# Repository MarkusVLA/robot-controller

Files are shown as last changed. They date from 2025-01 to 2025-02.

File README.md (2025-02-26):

# Robot Controller

## Overview
ESP32-S3 based robot controller designed for combat robots in the 150g weight class

The controller can control 2 DC-motors for vehicle movement and an ESC for the main weapon. The board also embeds a 3-axis gyroscope and accelerometer which can be used to improve vehicle handling or detect when the robot is flipped. Wireless control is enabled through an integrated 2.4GHz PCB-antenna supporting both WiFi and Bluetooth. 

## Schematic and Layout

<div style="display: flex; gap: 20px;">
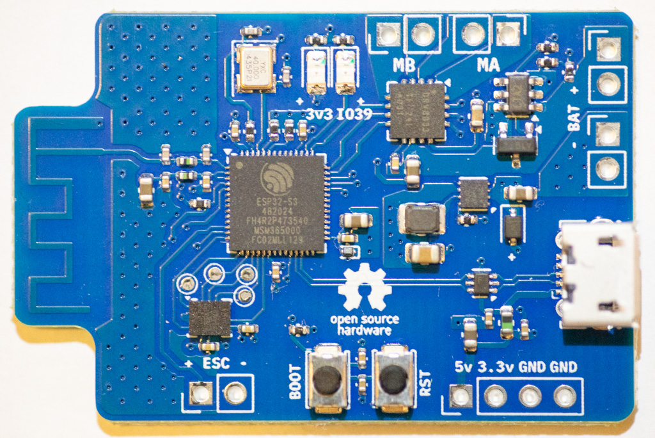
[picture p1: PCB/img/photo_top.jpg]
3D render of the top side
    
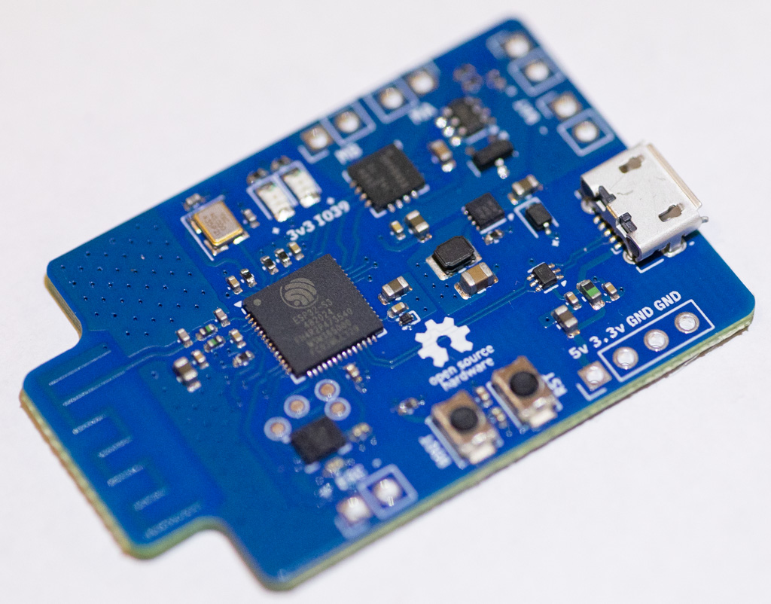
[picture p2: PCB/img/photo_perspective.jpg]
3D render perspective view
    
</div>

[View Schematic (PDF)](documentation/schematic.pdf)

## Firmware
The esp32 firmware is being developed in C using the ESP-IDF framework.
Installation and build instructions from: [ESP-IDF API reference](https://docs.espressif.com/projects/esp-idf/en/stable/esp32/api-reference/index.html)

[Comprehensive hardware documentation](documentation/Hardware_documentation.pdf)

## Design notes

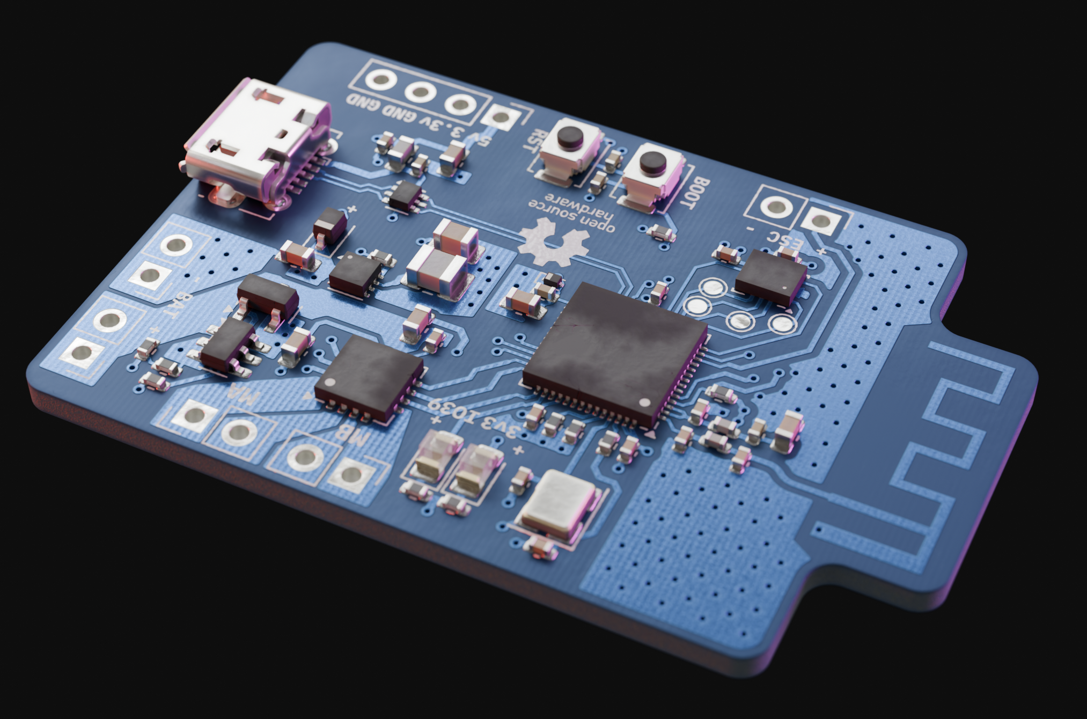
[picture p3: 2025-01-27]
PCB/img/render.png

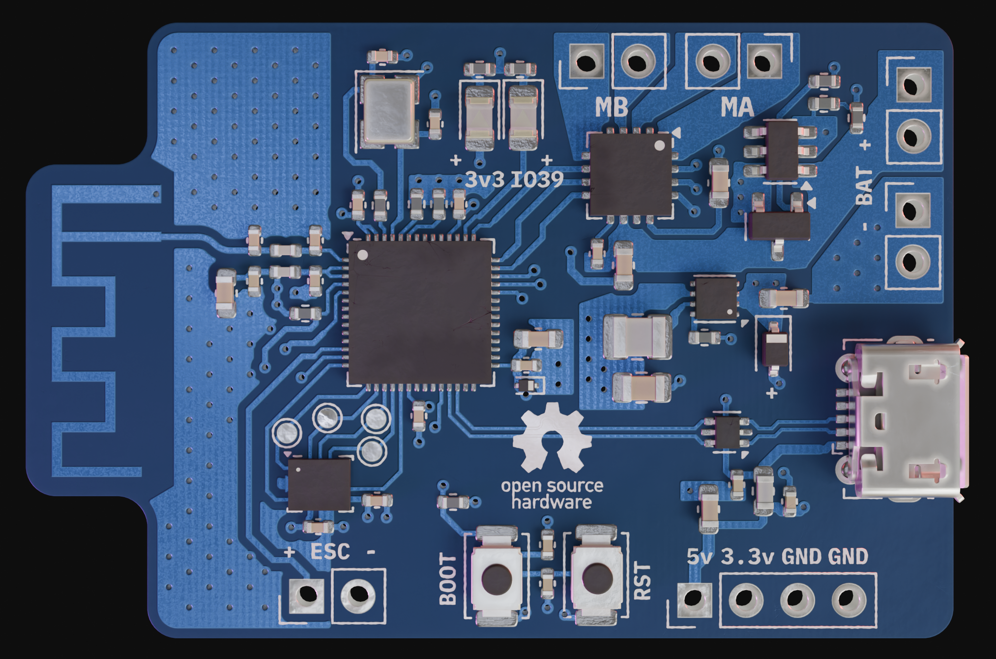
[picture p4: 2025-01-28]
PCB/img/render_top.png

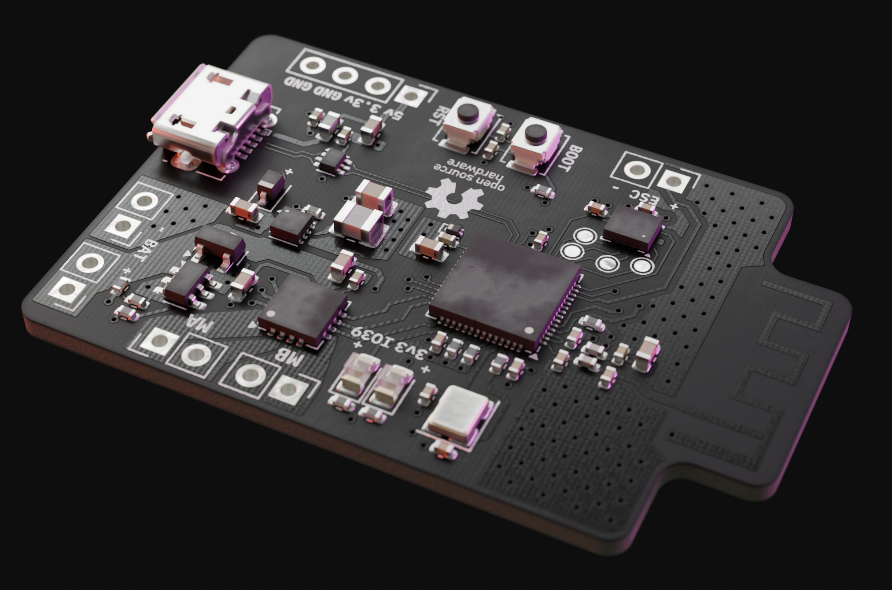
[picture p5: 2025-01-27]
PCB/img/render2.png

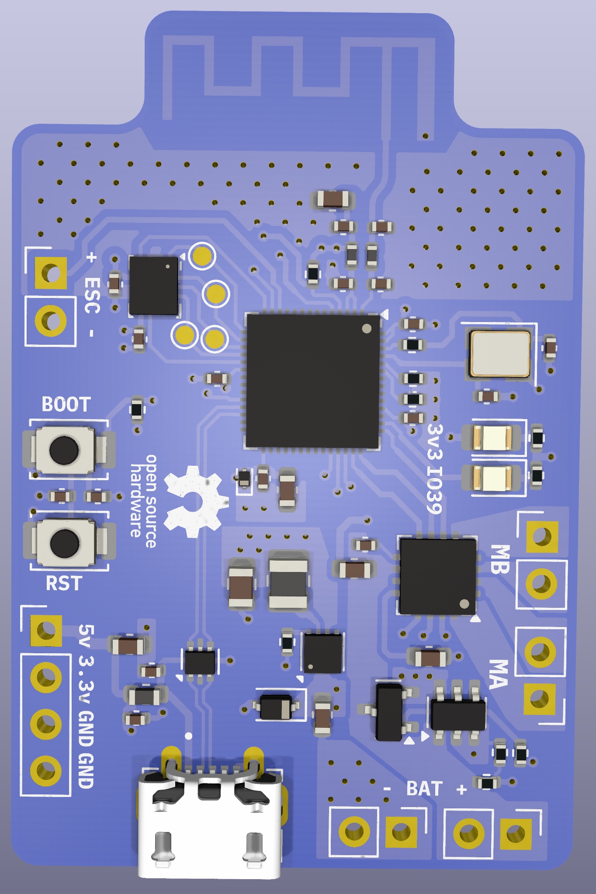
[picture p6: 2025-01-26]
PCB/img/layout.jpg

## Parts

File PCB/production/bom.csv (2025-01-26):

Designator | Footprint | Quantity | Value | LCSC Part #
AE2 | Texas_SWRA117D_2.4GHz_Left | 1 | Antenna_Shield
C1, C13, C14, C2, C30, C32, C33, C35, C36, C37, C8, C9 | 0402 | 12 | 100n
C10, C12, C34, C39, C5 | 0603 | 5 | 10u
C11 | 0603 | 1 | 2.2u
C27, C28 | 0402 | 2 | 22p
C29, C31 | 0402 | 2 | 3.3p
C6 | 0805 | 1 | 22u
C7 | 0402 | 1 | 10n
D1, D4 | 0805 | 2 | LED | C205445
D3 | D_SOD-323 | 1 | BAT60A
D5 | D_SOD-923 | 1 | SZESD9B5.0ST5G
J1 | USB_Micro-B_Molex-105017-0001 | 1 | USB_B_Micro
J10, J3, J4, J5, J6 | PinHeader_1x02_P2.54mm_Vertical | 5 | Conn_01x02
J2 | PinHeader_1x04_P2.54mm_Vertical | 1 | Conn_01x04
L1 | 1008 | 1 | 2.2u
L2 | 0603 | 1 | 2.2n
L5, L6 | 0402 | 2 | 2.2n
Q1 | SOT-23 | 1 | AO3401A
R1, R5 | 0402 | 2 | 1k | C163928
R12 | 0402 | 1 | 10
R13, R14, R2, R7, R8 | 0402 | 5 | 10k
R3 | 0402 | 1 | 470k
R4 | 0402 | 1 | 100k
R6 | 0402 | 1 | 15k
SW3 | SW_Push_SPST_NO_Alps_SKRK | 1 | Reset | C115357
SW4 | SW_Push_SPST_NO_Alps_SKRK | 1 | Boot | C115357
TP1, TP2, TP3, TP4 | TestPoint_Pad_D1.0mm | 4 | TestPoint
U1 | LGA-14_3x2.5mm_P0.5mm_LayoutBorder3x4y | 1 | LSM6DS3
U2 | TSOT-23-6 | 1 | LTC4412xS6
U3 | SOT-666 | 1 | USBLC6-2P6
U4 | WSON-8-1EP_2x2mm_P0.5mm_EP0.9x1.6mm_ThermalVias | 1 | TPS62172DSG
U5 | Texas_RTY_WQFN-16-1EP_4x4mm_P0.65mm_EP2.1x2.1mm_ThermalVias | 1 | DRV8833RTY
U7 | QFN-56-1EP_7x7mm_P0.4mm_EP5.6x5.6mm | 1 | ESP32-S3
Y2 | Crystal_SMD_3225-4Pin_3.2x2.5mm | 1 | 40MHz

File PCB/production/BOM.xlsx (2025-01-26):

Designator | Footprint | Quantity | Value | LCSC Part #
C1, C13, C14, C2, C30, C32, C33, C35, C36, C37, C8, C9 | 402 | 12 | 100n | C1525
C10, C12, C34, C39, C5 | 603 | 5 | 10u | C70225
C11 | 603 | 1 | 2.2u | C57895
C27, C28 | 402 | 2 | 22p | C1555
C29, C31 | 402 | 2 | 3.3p | C57895
C6 | 805 | 1 | 22u | C45783
C7 | 402 | 1 | 10n | C15195
D1, D4 | 805 | 2 | LED | C2295
D3 | D_SOD-323 | 1 | BAT60A | C3018529
D5 | D_SOD-923 | 1 | SZESD9B5.0ST5G | C328101
J1 | CUI_UJ2-MIBH2-4-SMT-TR | 1 | UJ2-MIBH2-4-SMT-TR | C91146
L1 | 1008 | 1 | 2.2u | C23894
L2 | 603 | 1 | 2.2n | C113061
L5, L6 | 402 | 2 | 2.2n | C86061
Q1 | SOT-23 | 1 | AO3401A | C181091
R1, R5 | 402 | 2 | 1k | C11702
R12 | 402 | 1 | 10 | C159870
R13, R14, R2, R7, R8 | 402 | 5 | 10k | C25531
R3 | 402 | 1 | 470k | C25562
R4 | 402 | 1 | 100k | C25741
R6 | 402 | 1 | 15k | C25543
SW3 | SW_Push_SPST_NO_Alps_SKRK | 1 | Reset | C115357
SW4 | SW_Push_SPST_NO_Alps_SKRK | 1 | Boot | C115357
U1 | LGA-14_3x2.5mm_P0.5mm_LayoutBorder3x4y | 1 | LSM6DS3 | C95230
U2 | TSOT-23-6 | 1 | LTC4412xS6 | C514442
U3 | SOT-666 | 1 | USBLC6-2P6 | C15999
U4 | WSON-8-1EP_2x2mm_P0.5mm_EP0.9x1.6mm_ThermalVias | 1 | TPS62172DSG | C59873
U5 | Texas_RTY_WQFN-16-1EP_4x4mm_P0.65mm_EP2.1x2.1mm_ThermalVias | 1 | DRV8833RTY | C154936
U7 | QFN-56-1EP_7x7mm_P0.4mm_EP5.6x5.6mm | 1 | ESP32-S3 | C3013940
Y2 | Crystal_SMD_3225-4Pin_3.2x2.5mm | 1 | 40MHz | C9010

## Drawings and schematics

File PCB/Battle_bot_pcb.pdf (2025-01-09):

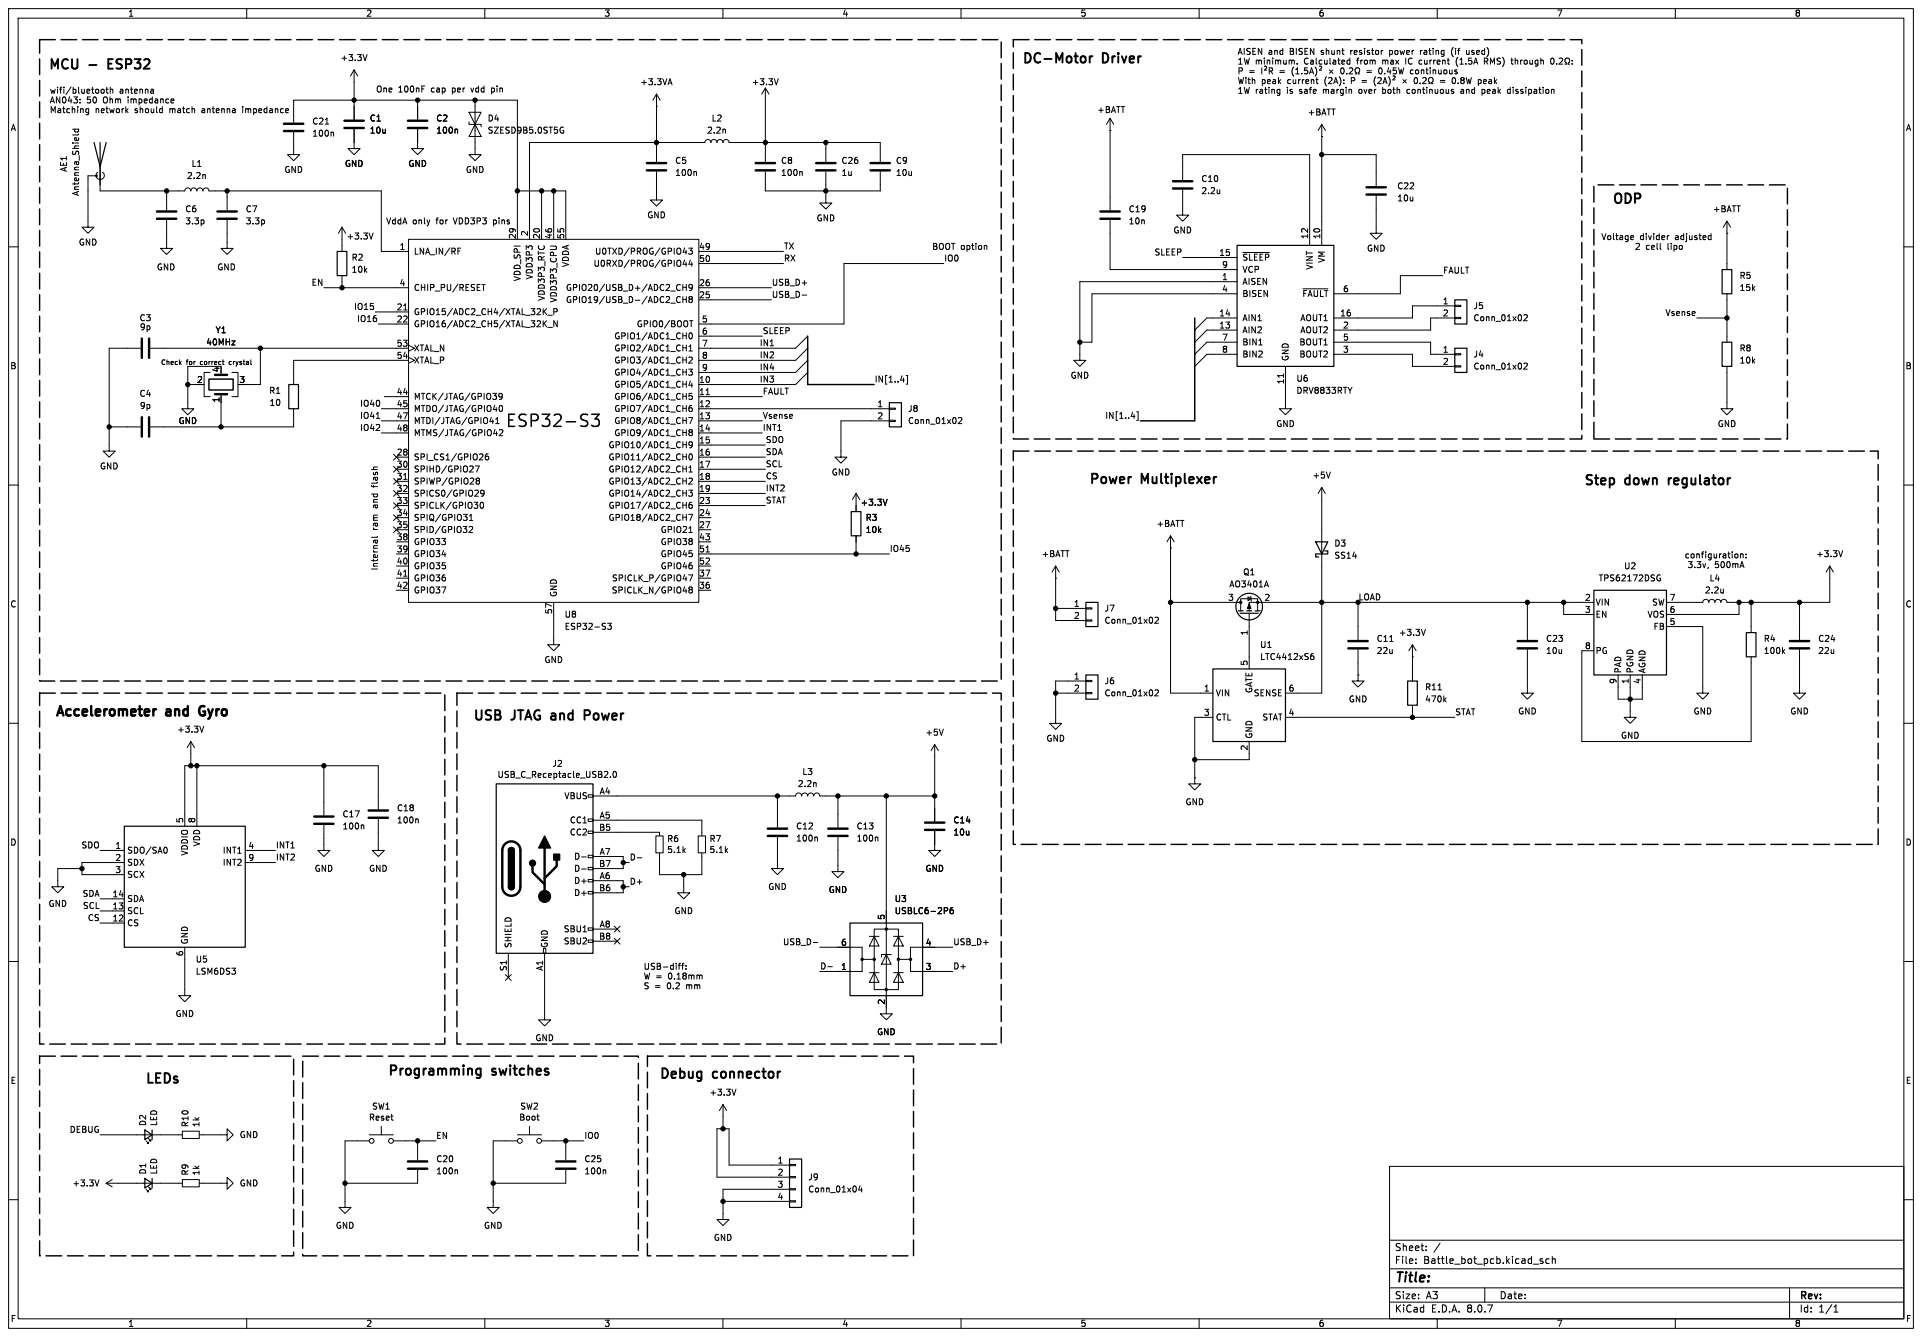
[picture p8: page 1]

One 100nF cap per vdd pin C1

Matching network should match antenna impedance

VddA only for VDD3P3 pins

2 VDD3P3_RTC 20 GPIO15/ADC2_CH4/XTAL_32K_P 21 GPIO16/ADC2_CH5/XTAL_32K_N 22 GPIO17/ADC2_CH6 23 GPIO18/ADC2_CH7 24 GPIO19/USB_D-/ADC2_CH8 25 GPIO20/USB_D+/ADC2_CH9 26 GPIO21 27 SPI_CS1/GPIO26 28 VDD_SPI 29 SPIHD/GPIO27 30 SPIWP/GPIO28 31 SPICS0/GPIO29 32 SPICLK/GPIO30 33 SPIQ/GPIO31 34 SPID/GPIO32 35 GPIO33 38 GPIO34 39 CHIP_PU/RESET 4 GPIO35 40 GPIO36 41 GPIO37 42 GPIO38 43 MTCK/JTAG/GPIO39 44 MTDO/JTAG/GPIO40 45 VDD3P3_CPU 46 MTDI/JTAG/GPIO41 47 MTMS/JTAG/GPIO42 48 U0TXD/PROG/GPIO43 49 GPIO0/BOOT 5 U0RXD/PROG/GPIO44 50 GPIO45 51 GPIO46 52 XTAL_N 53 XTAL_P 54 VDDA 55 GND 57 GPIO1/ADC1_CH0 6 GPIO2/ADC1_CH1 7 GPIO3/ADC1_CH2 8 GPIO4/ADC1_CH3 9 U8ESP32-S3

S = 0.2 mm Debug connector Internal ram and flash

SDO/SA0 1 CS 12 SCL 13 SDA 14 SDX 2 SCX 3

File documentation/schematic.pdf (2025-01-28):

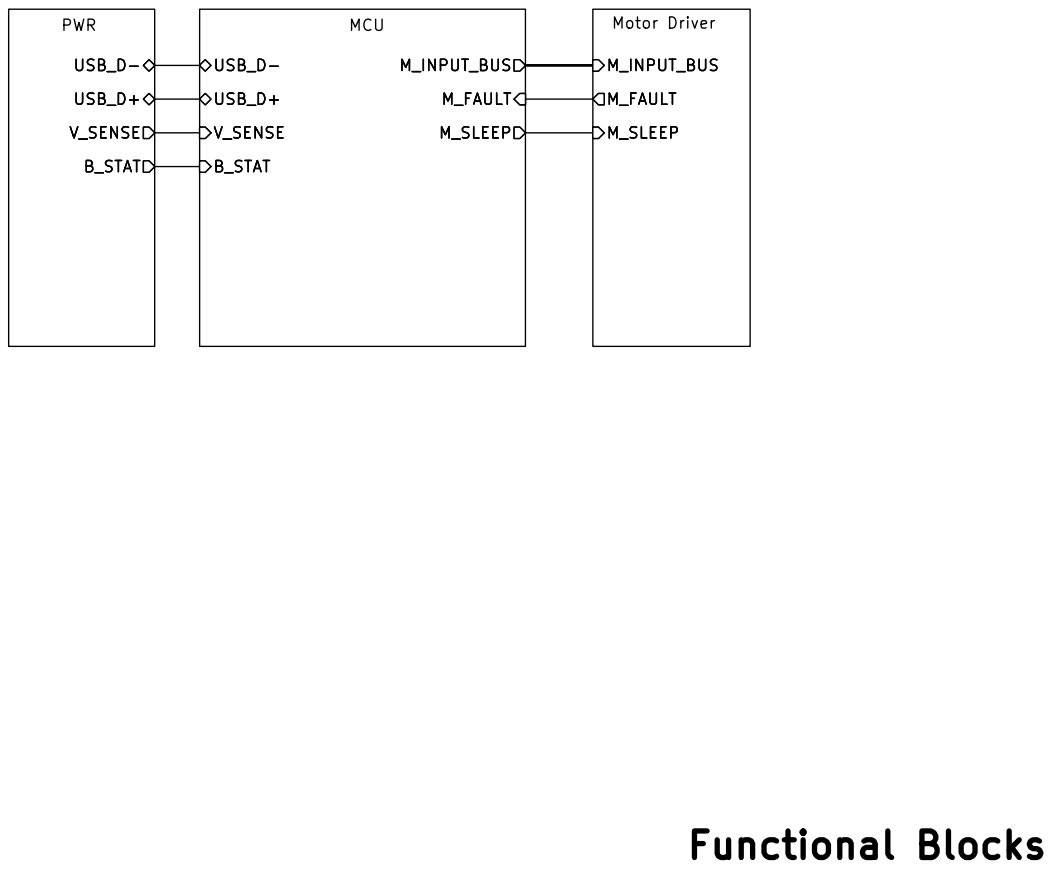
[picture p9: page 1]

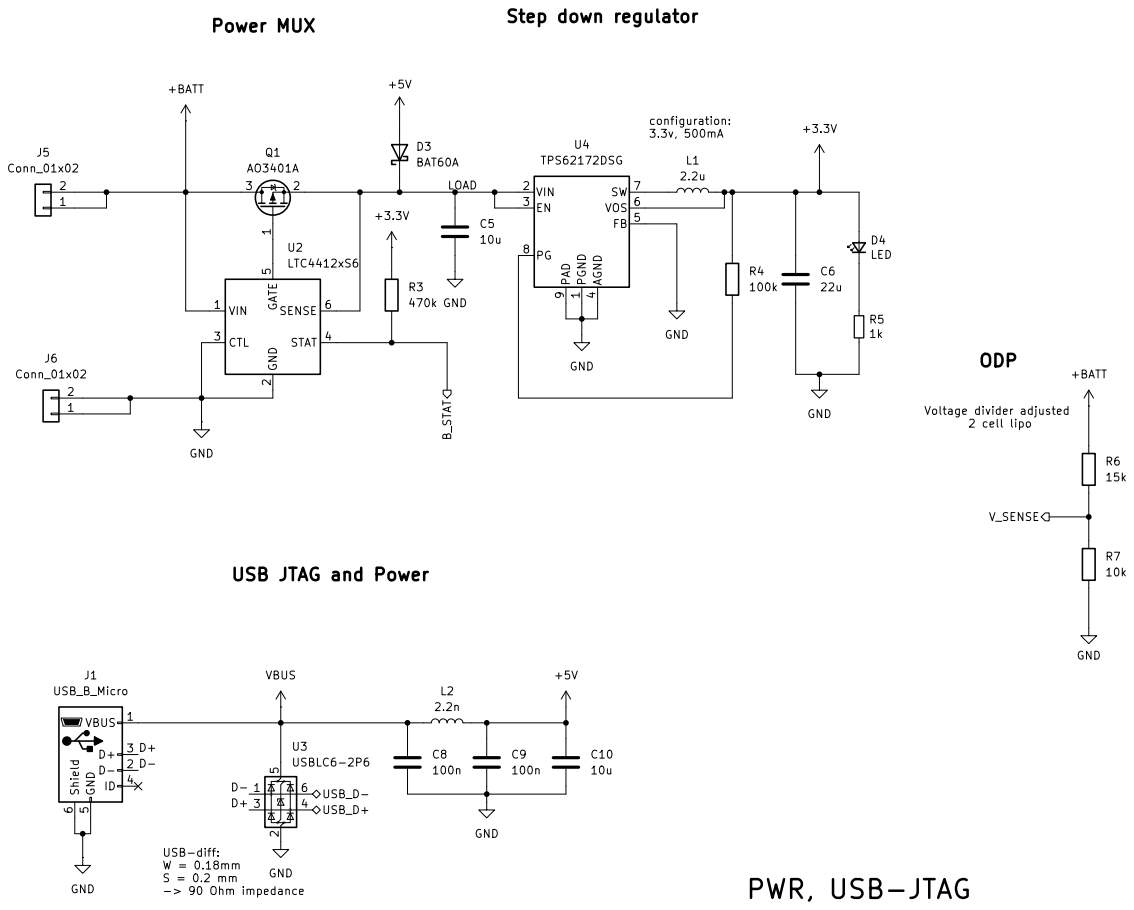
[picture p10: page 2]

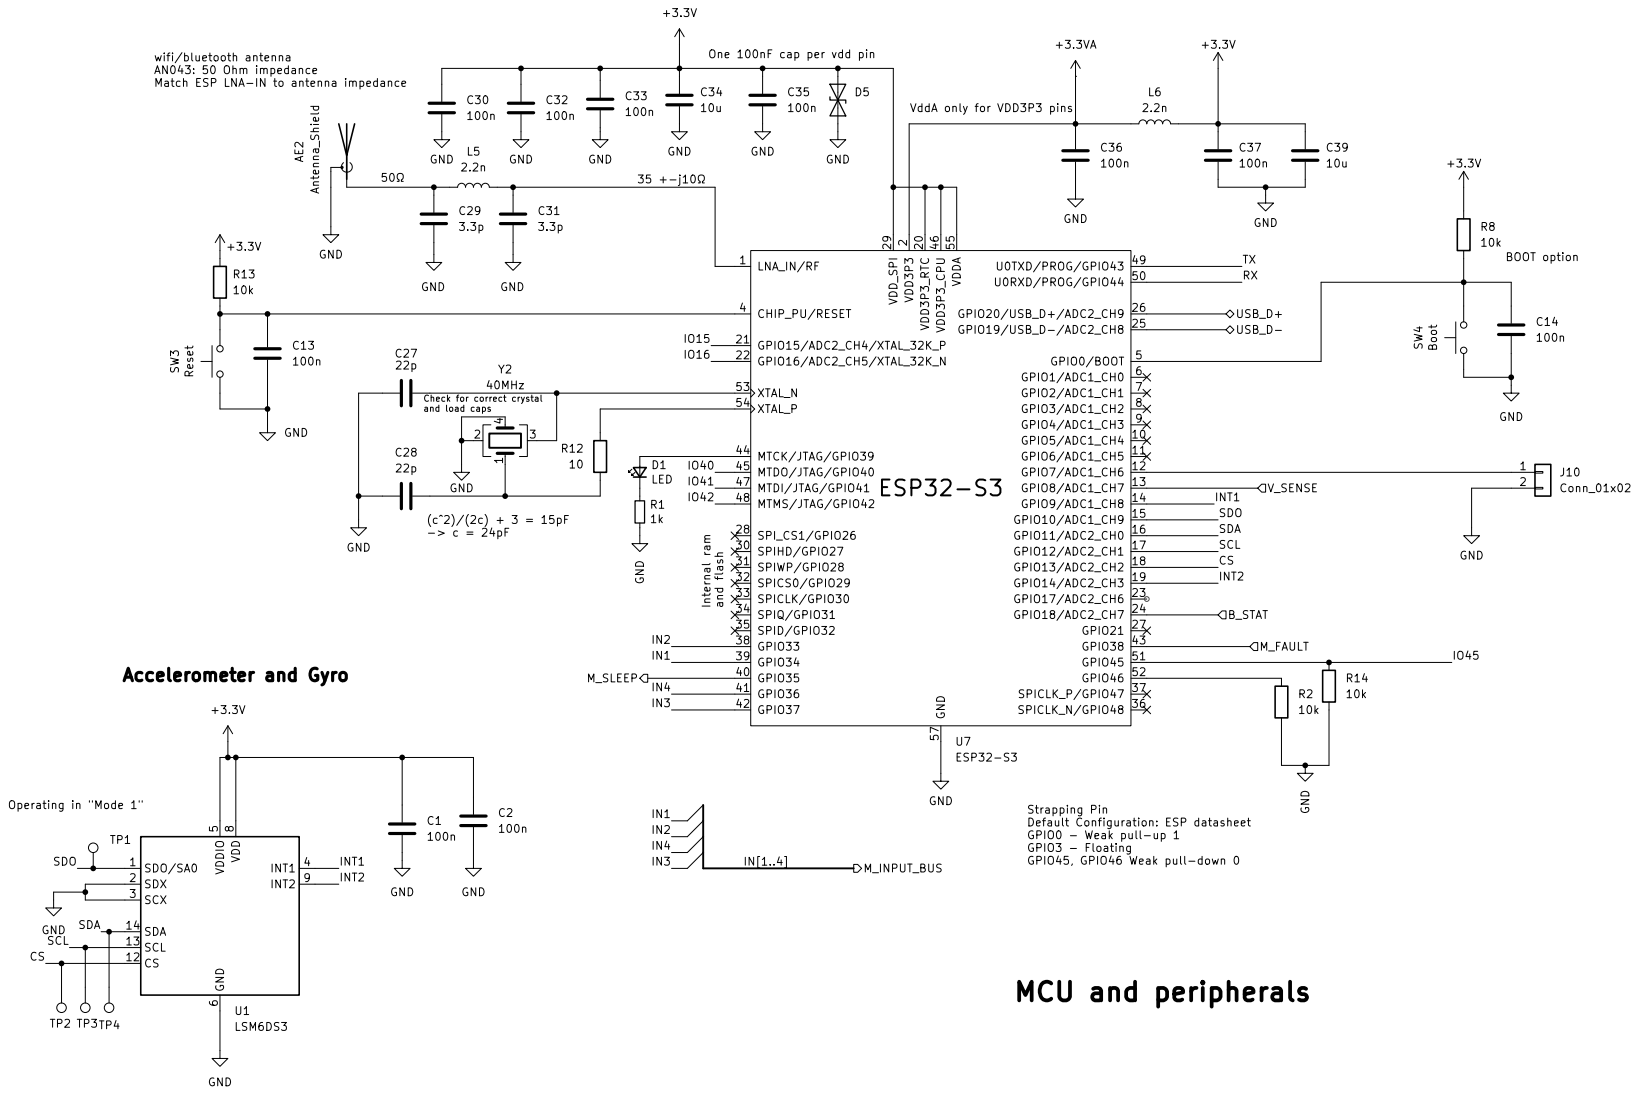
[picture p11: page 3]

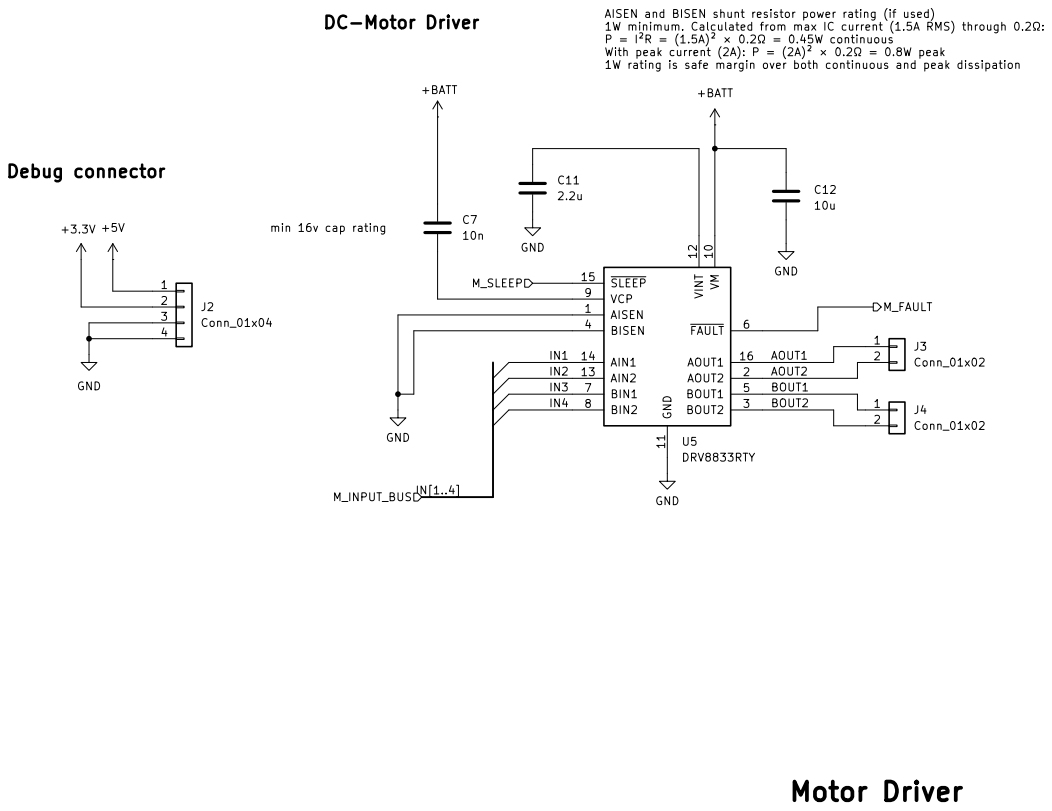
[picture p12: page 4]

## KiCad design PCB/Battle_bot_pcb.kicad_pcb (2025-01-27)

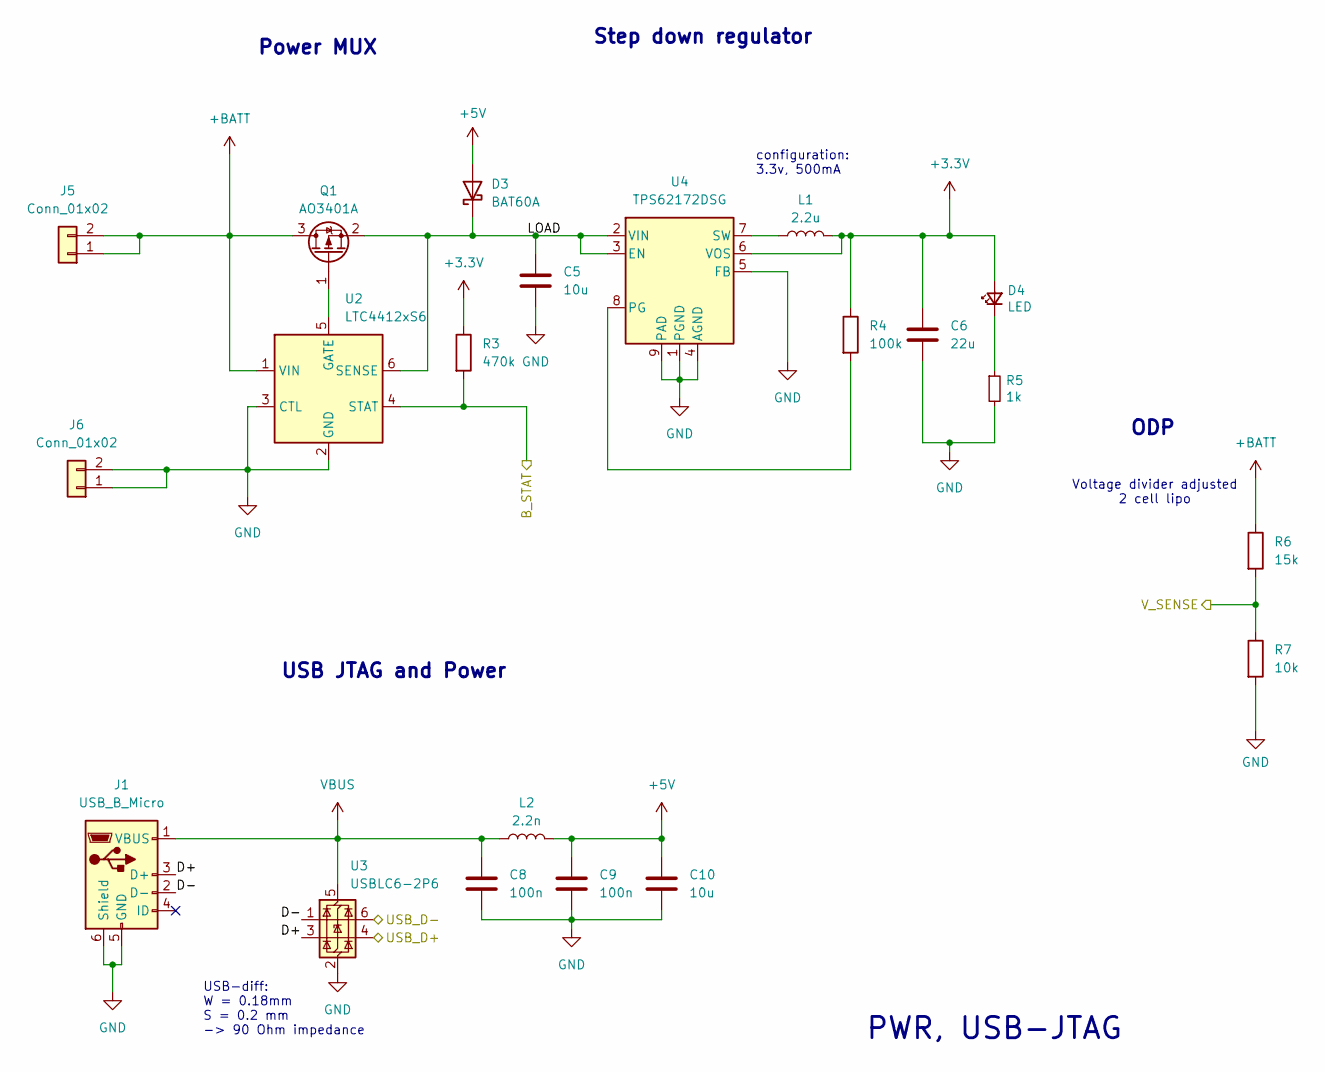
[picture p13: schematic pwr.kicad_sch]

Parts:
C5, C10: 10u; C_0603_1608Metric
C6: 22u; C_0805_2012Metric
C8, C9: 100n; C_0402_1005Metric
D3: BAT60A; D_SOD-323
D4: LED; LED_0805_2012Metric_Pad1.15x1.40mm_HandSolder; LCSC C205445
J1: USB_B_Micro; USB_Micro-B_Molex-105017-0001
J5, J6: Conn_01x02; PinHeader_1x02_P2.54mm_Vertical
L1: 2.2u; L_1008_2520Metric
L2: 2.2n; L_0603_1608Metric
Q1: AO3401A; SOT-23
R3: 470k; R_0402_1005Metric
R4: 100k; R_0402_1005Metric
R5: 1k; R_0402_1005Metric; LCSC C163928
R6: 15k; R_0402_1005Metric
R7: 10k; R_0402_1005Metric
U2: LTC4412xS6; TSOT-23-6
U3: USBLC6-2P6; SOT-666
U4: TPS62172DSG; WSON-8-1EP_2x2mm_P0.5mm_EP0.9x1.6mm_ThermalVias

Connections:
+3.3V: C6.1, D4.2 (A), L1.2, R3.1, R4.1, U4.6 (VOS); also elsewhere on the board
+5V: C9.1, C10.1, D3.2 (A), L2.2; also elsewhere on the board
+BATT: J5.1, J5.2, Q1.3 (D), R6.1, U2.1 (VIN); also elsewhere on the board
/MCU/B_STAT: R3.2, U2.4 (STAT); also elsewhere on the board
/MCU/USB_D+: U3.4 (I/O2); also elsewhere on the board
/MCU/USB_D-: U3.6 (I/O1); also elsewhere on the board
/MCU/V_SENSE: R6.2, R7.1; also elsewhere on the board
/PWR/D+: J1.3 (D+), U3.3 (I/O2)
/PWR/D-: J1.2 (D-), U3.1 (I/O1)
/PWR/LOAD: C5.1, D3.1 (K), Q1.2 (S), U2.6 (SENSE), U4.2 (VIN), U4.3 (EN)
GND: C5.2, C6.2, C8.2, C9.2, C10.2, J1.5 (GND), J1.6 (Shield), J6.1, J6.2, R5.2, R7.2, U2.2 (GND), U2.3 (CTL), U3.2 (GND), U4.1 (PGND), U4.4 (AGND), U4.5 (FB), U4.9 (PAD); also elsewhere on the board
unnamed: D4.1 (K), R5.1
unnamed: Q1.1 (G), U2.5 (GATE)
unnamed: R4.2, U4.8 (PG)
unnamed: L1.1, U4.7 (SW)
VBUS: C8.1, J1.1 (VBUS), L2.1, U3.5 (VBUS)

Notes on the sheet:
Power MUX
USB JTAG and Power
ODP
USB-diff: W = 0.18mm S = 0.2 mm -> 90 Ohm impedance
configuration: 3.3v, 500mA
PWR, USB-JTAG
Voltage divider adjusted 2 cell lipo
Step down regulator

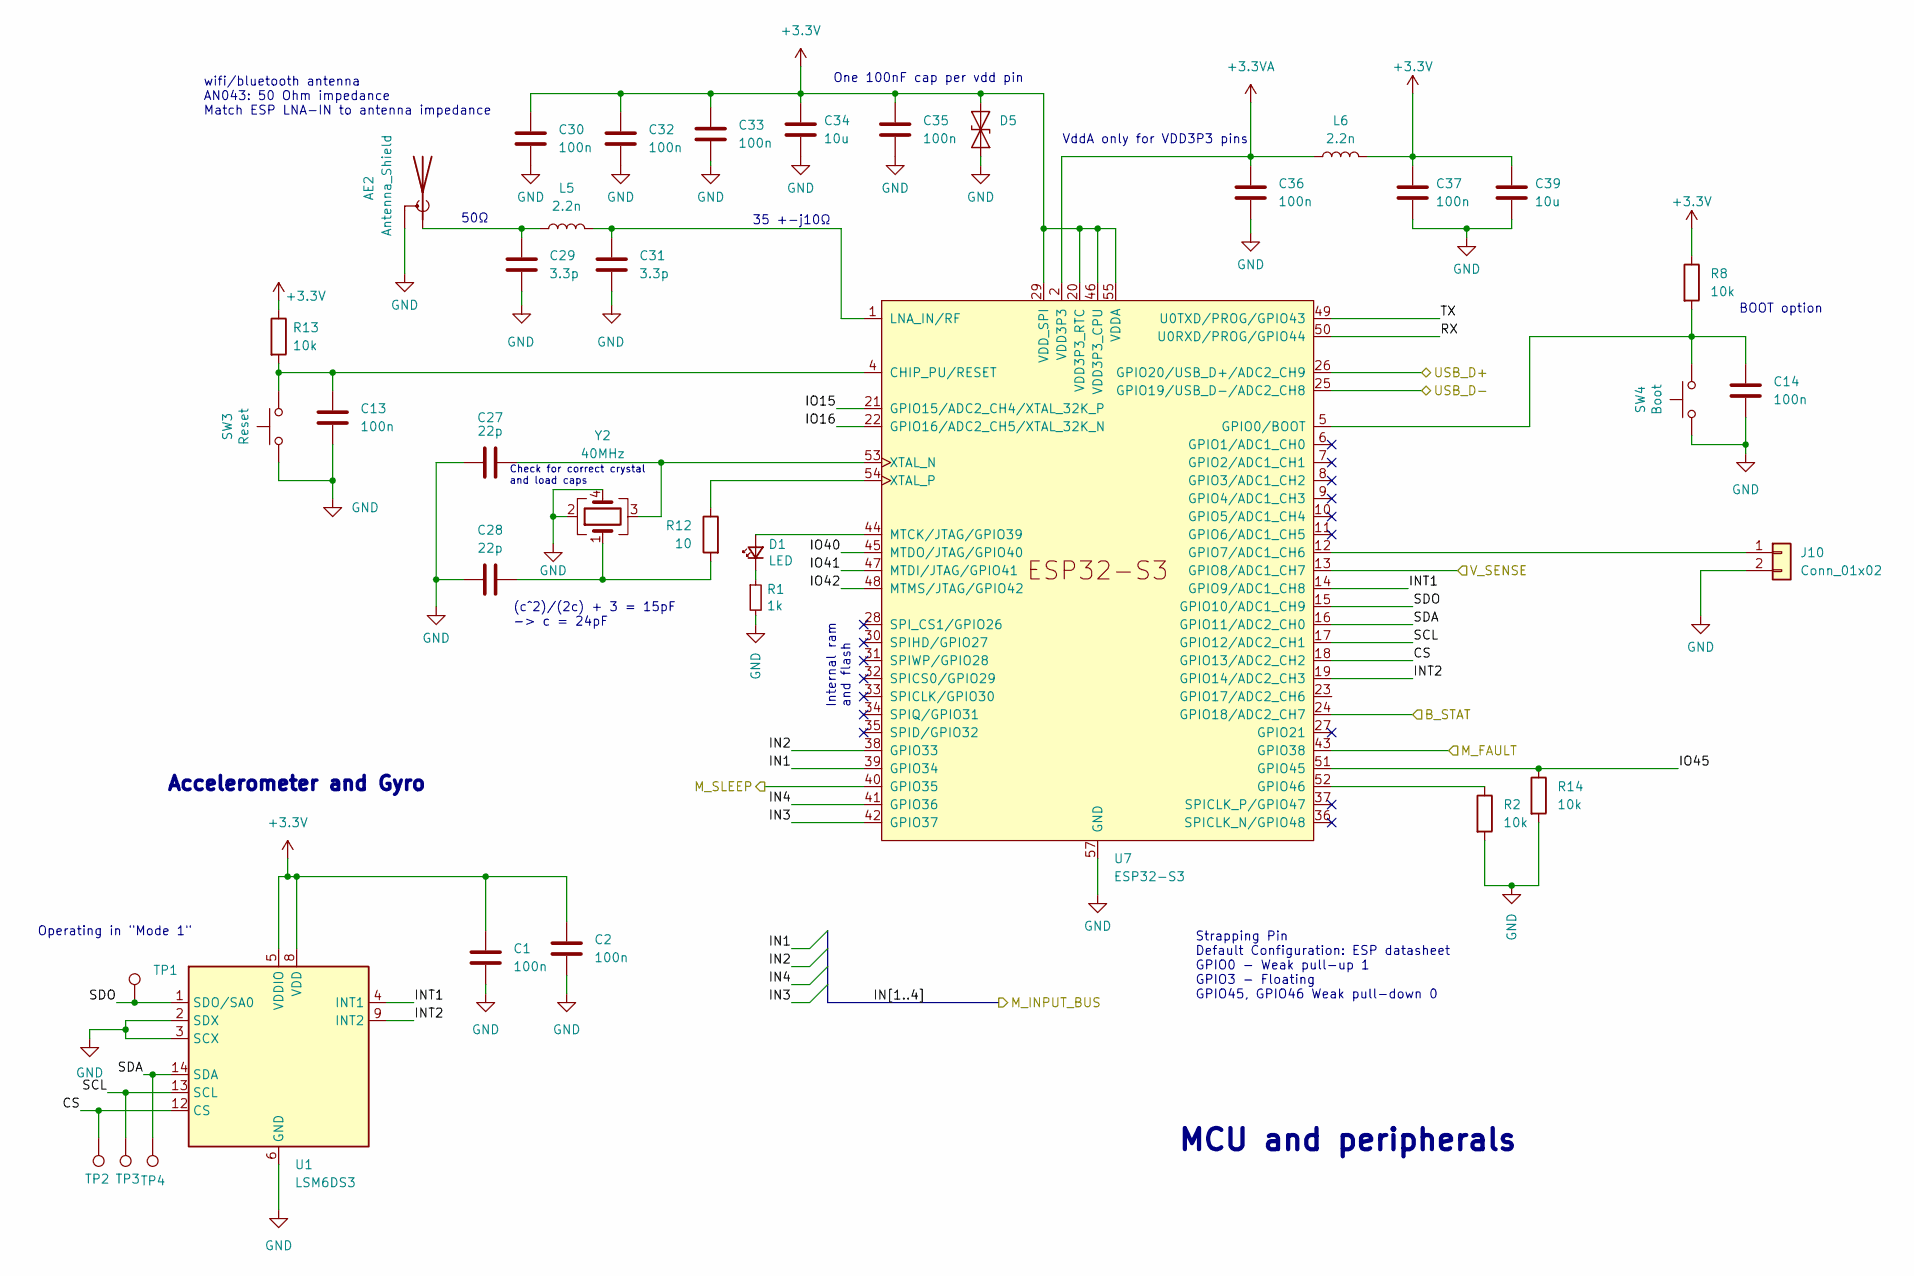
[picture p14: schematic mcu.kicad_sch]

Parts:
AE2: Antenna_Shield; Texas_SWRA117D_2.4GHz_Left
C1, C2, C13, C14, C30, C32, C33, C35, C36, C37: 100n; C_0402_1005Metric
C27, C28: 22p; C_0402_1005Metric
C29, C31: 3.3p; C_0402_1005Metric
C34, C39: 10u; C_0603_1608Metric
D1: LED; LED_0805_2012Metric_Pad1.15x1.40mm_HandSolder; LCSC C205445
D5: SZESD9B5.0ST5G; D_SOD-923
J10: Conn_01x02; PinHeader_1x02_P2.54mm_Vertical
L5, L6: 2.2n; L_0402_1005Metric
R1: 1k; R_0402_1005Metric; LCSC C163928
R2, R8, R13, R14: 10k; R_0402_1005Metric
R12: 10; R_0402_1005Metric
SW3: Reset; SW_Push_SPST_NO_Alps_SKRK; LCSC C115357
SW4: Boot; SW_Push_SPST_NO_Alps_SKRK; LCSC C115357
TP1, TP2, TP3, TP4: TestPoint; TestPoint_Pad_D1.0mm
U1: LSM6DS3; LGA-14_3x2.5mm_P0.5mm_LayoutBorder3x4y
U7: ESP32-S3; QFN-56-1EP_7x7mm_P0.4mm_EP5.6x5.6mm
Y2: 40MHz; Crystal_SMD_3225-4Pin_3.2x2.5mm

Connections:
+3.3V: C1.1, C2.1, C30.1, C32.1, C33.1, C34.1, C35.1, C37.1, C39.1, D5.2 (A2), L6.2, R8.1, R13.1, U1.5 (VDDIO), U1.8 (VDD), U7.20 (VDD3P3_RTC), U7.29 (VDD_SPI), U7.46 (VDD3P3_CPU), U7.55 (VDDA), U7.56 (VDDA); also elsewhere on the board
+3.3VA: C36.1, L6.1, U7.2 (VDD3P3), U7.3 (VDD3P3)
/IO/IN1: U7.39 (GPIO34); also elsewhere on the board
/IO/IN2: U7.38 (GPIO33); also elsewhere on the board
/IO/IN3: U7.42 (GPIO37); also elsewhere on the board
/IO/IN4: U7.41 (GPIO36); also elsewhere on the board
/IO/M_FAULT: U7.43 (GPIO38); also elsewhere on the board
/IO/M_SLEEP: U7.40 (GPIO35); also elsewhere on the board
/MCU/B_STAT: U7.24 (GPIO18/ADC2_CH7); also elsewhere on the board
/MCU/CS: TP2.1, U1.12 (CS), U7.18 (GPIO13/ADC2_CH2)
/MCU/INT1: U1.4 (INT1), U7.14 (GPIO9/ADC1_CH8)
/MCU/INT2: U1.9 (INT2), U7.19 (GPIO14/ADC2_CH3)
/MCU/IO15: U7.21 (GPIO15/ADC2_CH4/XTAL_32K_P)
/MCU/IO16: U7.22 (GPIO16/ADC2_CH5/XTAL_32K_N)
/MCU/IO40: U7.45 (MTDO/JTAG/GPIO40)
/MCU/IO41: U7.47 (MTDI/JTAG/GPIO41)
/MCU/IO42: U7.48 (MTMS/JTAG/GPIO42)
/MCU/IO45: R14.1, U7.51 (GPIO45)
/MCU/RX: U7.50 (U0RXD/PROG/GPIO44)
/MCU/SCL: TP3.1, U1.13 (SCL), U7.17 (GPIO12/ADC2_CH1)
/MCU/SDA: TP4.1, U1.14 (SDA), U7.16 (GPIO11/ADC2_CH0)
/MCU/SDO: TP1.1, U1.1 (SDO/SA0), U7.15 (GPIO10/ADC1_CH9)
/MCU/TX: U7.49 (U0TXD/PROG/GPIO43)
/MCU/USB_D+: U7.26 (GPIO20/USB_D+/ADC2_CH9); also elsewhere on the board
/MCU/USB_D-: U7.25 (GPIO19/USB_D-/ADC2_CH8); also elsewhere on the board
/MCU/V_SENSE: U7.13 (GPIO8/ADC1_CH7); also elsewhere on the board
GND: AE2.2 (Shield), C1.2, C2.2, C13.2, C14.2, C27.1, C28.1, C29.2, C30.2, C31.2, C32.2, C33.2, C34.2, C35.2, C36.2, C37.2, C39.2, D5.1 (A1), J10.2, R1.2, R2.2, R14.2, SW3.2, SW4.2, U1.2 (SDX), U1.3 (SCX), U1.6 (GND), U1.7 (GND), U7.57 (GND), Y2.2, Y2.4; also elsewhere on the board
unnamed: AE2.1 (A), C29.1, L5.1
unnamed: C28.2, R12.2, Y2.1
unnamed: D1.2 (A), U7.44 (MTCK/JTAG/GPIO39)
unnamed: D1.1 (K), R1.1
unnamed: J10.1, U7.12 (GPIO7/ADC1_CH6)
unnamed: C13.1, R13.2, SW3.1, U7.4 (CHIP_PU/RESET)
unnamed: C14.1, R8.2, SW4.1, U7.5 (GPIO0/BOOT)
unnamed: R2.1, U7.52 (GPIO46)
unnamed: C31.1, L5.2, U7.1 (LNA_IN/RF)
unnamed: C27.2, U7.53 (XTAL_N), Y2.3
unnamed: R12.1, U7.54 (XTAL_P)

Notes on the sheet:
Check for correct crystal and load caps
Internal ram and flash
MCU and peripherals
(c^2)/(2c) + 3 = 15pF -> c = 24pF
Accelerometer and Gyro
35 +-j10Ω
Operating in "Mode 1"
VddA only for VDD3P3 pins
One 100nF cap per vdd pin
50Ω
BOOT option
wifi/bluetooth antenna AN043: 50 Ohm impedance Match ESP LNA-IN to antenna impedance
Strapping Pin Default Configuration: ESP datasheet GPIO0 - Weak pull-up 1 GPIO3 - Floating GPIO45, GPIO46 Weak pull-down 0

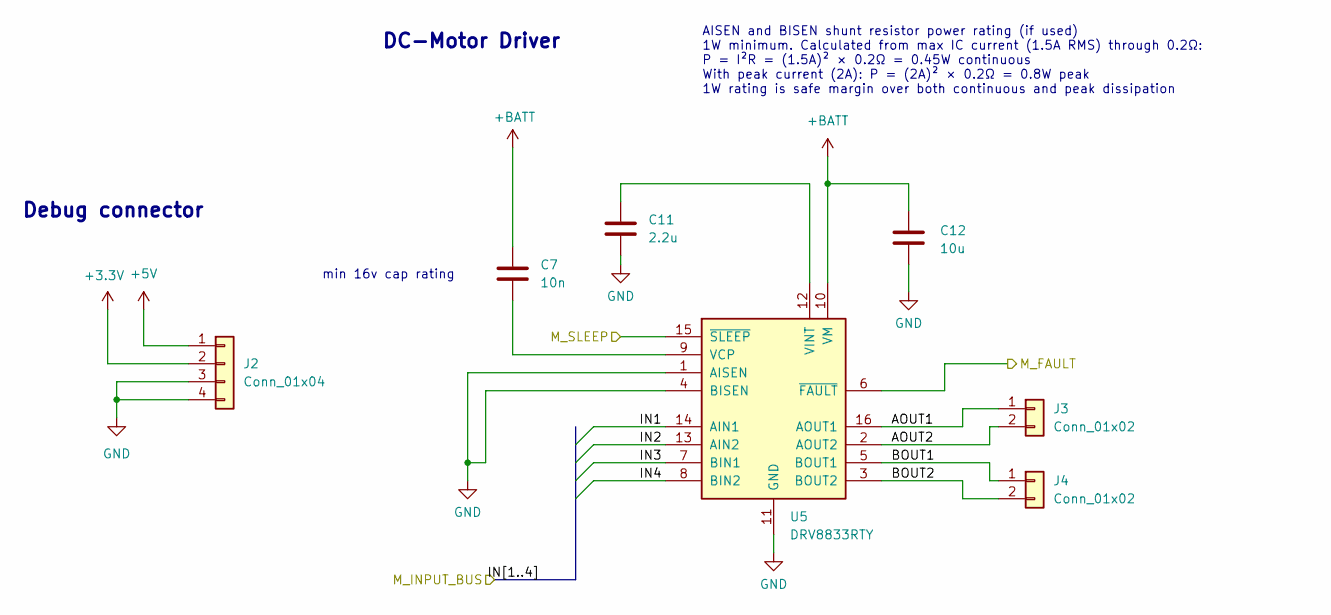
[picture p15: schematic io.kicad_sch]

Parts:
C7: 10n; C_0402_1005Metric
C11: 2.2u; C_0603_1608Metric
C12: 10u; C_0603_1608Metric
J2: Conn_01x04; PinHeader_1x04_P2.54mm_Vertical
J3, J4: Conn_01x02; PinHeader_1x02_P2.54mm_Vertical
U5: DRV8833RTY; Texas_RTY_WQFN-16-1EP_4x4mm_P0.65mm_EP2.1x2.1mm_ThermalVias

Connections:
+3.3V: J2.2; also elsewhere on the board
+5V: J2.1; also elsewhere on the board
+BATT: C7.1, C12.1, U5.10 (VM); also elsewhere on the board
/IO/AOUT1: J3.1, U5.16 (AOUT1)
/IO/AOUT2: J3.2, U5.2 (AOUT2)
/IO/BOUT1: J4.1, U5.5 (BOUT1)
/IO/BOUT2: J4.2, U5.3 (BOUT2)
/IO/IN1: U5.14 (AIN1); also elsewhere on the board
/IO/IN2: U5.13 (AIN2); also elsewhere on the board
/IO/IN3: U5.7 (BIN1); also elsewhere on the board
/IO/IN4: U5.8 (BIN2); also elsewhere on the board
/IO/M_FAULT: U5.6 (~FAULT); also elsewhere on the board
/IO/M_SLEEP: U5.15 (~SLEEP); also elsewhere on the board
GND: C11.2, C12.2, J2.3, J2.4, U5.1 (AISEN), U5.4 (BISEN), U5.11 (GND), U5.17 (GND); also elsewhere on the board
unnamed: C7.2, U5.9 (VCP)
unnamed: C11.1, U5.12 (VINT)

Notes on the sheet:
min 16v cap rating
Debug connector
AISEN and BISEN shunt resistor power rating (if used) 1W minimum. Calculated from max IC current (1.5A RMS) through 0.2Ω: P = I²R = (1.5A)² × 0.2Ω = 0.45W continuous With peak current (2A): P = (2A)² × 0.2Ω = 0.8W peak 1W rating is safe margin over both continuous and peak dissipation
DC-Motor Driver

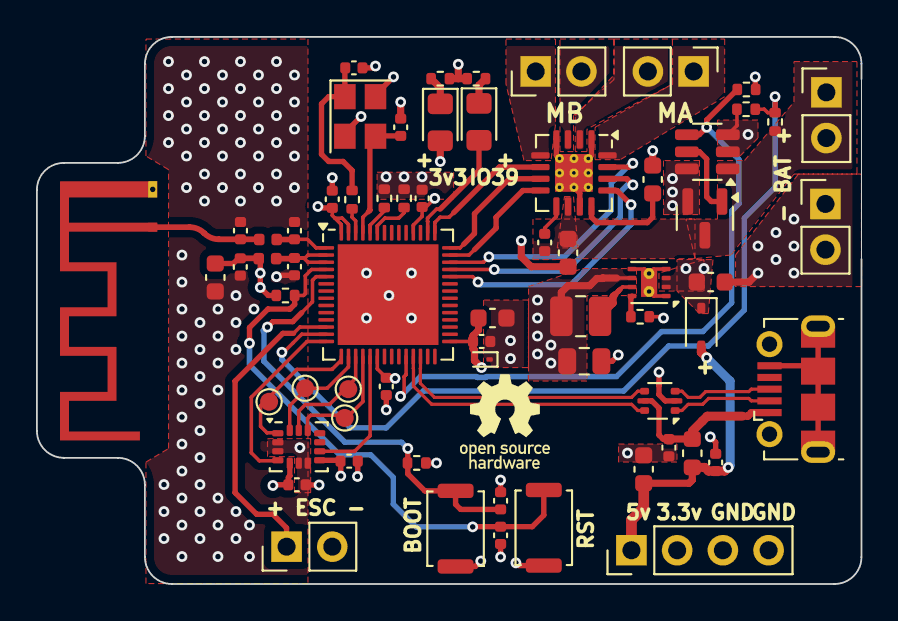
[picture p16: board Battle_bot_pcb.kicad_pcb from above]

Board: 4 copper layers, 45.8 x 30.4 mm, 65 parts (0 on the bottom side), 47 nets.

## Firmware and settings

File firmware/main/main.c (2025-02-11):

#include <driver/gpio.h>
#include <freertos/FreeRTOS.h>
#include <esp_event.h>
#include <nvs_flash.h>
#include <esp_log.h>

#include "wifi_api.h"
#include "rest_api.h"
#include "motor_api.h"
#include "sensor_api.h"
#include "io_config.h"

// Private config should include the defenitions:
// WIFI_SSID and WIFI_PASSWORD
#include "private_config.h" 

#define TAG "main"

void app_main(void) {
    gpio_config(&io_config);

    init_wifi();
    esp_err_t ret = connect_wifi(WIFI_SSID, WIFI_PASSWORD);
    if (ret != ESP_OK) {
        ESP_LOGE(TAG, "Failed to connect to WiFi");
        /*return;*/
        ESP_LOGI(TAG, "Continuing to main loop wihtout WiFi connection");
    }

    esp_netif_ip_info_t ip_info;
    esp_netif_get_ip_info(esp_netif_get_handle_from_ifkey("WIFI_STA"), &ip_info);
    ESP_LOGI(TAG, "Server running on address: " IPSTR, IP2STR(&ip_info.ip));

    // Init REST API
    httpd_handle_t server_handle = start_webserver();

    ret = init_motor_config();
    if (ret != ESP_OK) {
        ESP_LOGE(TAG, "Failed to initalize motor config");
        return;
    }

    ret = init_sensors();
    if (ret != ESP_OK) {
        ESP_LOGE(TAG, "Failed to initalize sensors");
    }

    int running = 1;
    while(running) {
        vTaskDelay(pdMS_TO_TICKS(250));
        set_motor_a(MOTOR_FORWARD, 512); // Motor A forwards at 50% speed;
    }

    stop_webserver(server_handle);
    deinit_wifi();

}

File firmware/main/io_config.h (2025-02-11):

// GPIO pin definitions 

#pragma once

#include "driver/gpio.h"

#define LED_PIN GPIO_NUM_39

#define MOTOR_A_IN1     GPIO_NUM_34
#define MOTOR_A_IN2     GPIO_NUM_33
#define MOTOR_B_IN1     GPIO_NUM_37
#define MOTOR_B_IN2     GPIO_NUM_36

#define MOTOR_SLEEP     GPIO_NUM_35 

// Io configuration structure. 
extern gpio_config_t io_config;

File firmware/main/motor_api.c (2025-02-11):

#include "motor_api.h"
#include "driver/ledc.h" // PWM for motor speed
#include "io_config.h"
#include "esp_log.h"

#define TAG "Motor Driver"

static const ledc_timer_config_t motor_timer_config = {
    .speed_mode = LEDC_LOW_SPEED_MODE,
    .duty_resolution = LEDC_TIMER_10_BIT,
    .timer_num = LEDC_TIMER_0,
    .freq_hz = 1000,                // 1kHz Ctrl signal for motors
    .clk_cfg = LEDC_AUTO_CLK,
};

static const ledc_channel_config_t motor_channels[4] = {

    {
        .gpio_num = MOTOR_A_IN1,
        .speed_mode = LEDC_LOW_SPEED_MODE,
        .channel = LEDC_CHANNEL_0,
        .timer_sel = LEDC_TIMER_0,
        .intr_type = LEDC_INTR_DISABLE,
        .duty = 0,
        .hpoint = 0 
    },

    {
        .gpio_num = MOTOR_A_IN2,
        .speed_mode = LEDC_LOW_SPEED_MODE,
        .channel = LEDC_CHANNEL_1,
        .timer_sel = LEDC_TIMER_0,
        .intr_type = LEDC_INTR_DISABLE,
        .duty = 0,
        .hpoint = 0 
    },

    {
        .gpio_num = MOTOR_B_IN1,
        .speed_mode = LEDC_LOW_SPEED_MODE,
        .channel = LEDC_CHANNEL_2,
        .timer_sel = LEDC_TIMER_0,
        .intr_type = LEDC_INTR_DISABLE,
        .duty = 0,
        .hpoint = 0 
    },

    {
        .gpio_num = MOTOR_B_IN2,
        .speed_mode = LEDC_LOW_SPEED_MODE,
        .channel = LEDC_CHANNEL_3,
        .timer_sel = LEDC_TIMER_0,
        .intr_type = LEDC_INTR_DISABLE,
        .duty = 0,
        .hpoint = 0 
    },
};

esp_err_t init_motor_config(void) {
    esp_err_t ret;
    ret = ledc_timer_config(&motor_timer_config);
    
    if (ret != ESP_OK){
        return ret;
    } 

    for (int i = 0; i < 4; i++){
        ret = ledc_channel_config(&motor_channels[i]);
        if (ret != ESP_OK){
            ESP_LOGE(TAG, "Failed to init motor input %d", i);
            return ret;
        }
    }

    return ESP_OK;
}

/*esp_err_t test_motor_a(uint32_t duty) { */
/*    esp_err_t ret = ledc_set_duty(LEDC_LOW_SPEED_MODE, LEDC_CHANNEL_0, duty);*/
/**/
/*    if (ret != ESP_OK){*/
/*        return ret;*/
/*    }*/
/**/
/*    ret = ledc_update_duty(LEDC_LOW_SPEED_MODE, LEDC_CHANNEL_0);*/
/*    return ret;*/
/*}*/


esp_err_t set_motor_speed(int motor_num, motor_direction_t direction, uint32_t duty) {
    esp_err_t ret = ESP_OK;
    int channel_offset = motor_num * 2;  // 0 for motor A, 2 for motor B
    
    switch (direction) {
        case MOTOR_FORWARD:
            // Set IN1 to duty and IN2 to 0
            ret = ledc_set_duty(LEDC_LOW_SPEED_MODE, motor_channels[channel_offset].channel, duty);
            if (ret != ESP_OK) return ret;
            ret = ledc_set_duty(LEDC_LOW_SPEED_MODE, motor_channels[channel_offset + 1].channel, 0);
            if (ret != ESP_OK) return ret;
            break;
            
        case MOTOR_BACKWARD:
            // Set IN1 to 0 and IN2 to duty
            ret = ledc_set_duty(LEDC_LOW_SPEED_MODE, motor_channels[channel_offset].channel, 0);
            if (ret != ESP_OK) return ret;
            ret = ledc_set_duty(LEDC_LOW_SPEED_MODE, motor_channels[channel_offset + 1].channel, duty);
            if (ret != ESP_OK) return ret;
            break;
            
        case MOTOR_STOP:
            // Set both pins to 0
            ret = ledc_set_duty(LEDC_LOW_SPEED_MODE, motor_channels[channel_offset].channel, 0);
            if (ret != ESP_OK) return ret;
            ret = ledc_set_duty(LEDC_LOW_SPEED_MODE, motor_channels[channel_offset + 1].channel, 0);
            if (ret != ESP_OK) return ret;
            break;
    }
    
    ret = ledc_update_duty(LEDC_LOW_SPEED_MODE, motor_channels[channel_offset].channel);

    if (ret != ESP_OK) {
        ESP_LOGE(TAG, "Failed to set motor speed");
        return ret;
    }
    
    ret = ledc_update_duty(LEDC_LOW_SPEED_MODE, motor_channels[channel_offset + 1].channel);
    
    return ret;
}

esp_err_t set_motor_a(motor_direction_t direction, uint32_t duty) {
    return set_motor_speed(0, direction, duty);
}

esp_err_t set_motor_b(motor_direction_t direction, uint32_t duty) {
    return set_motor_speed(1, direction, duty);
}

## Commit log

2025-01-07 Adding files to git
    [Battle_bot_pcb.kicad_pcb, Battle_bot_pcb.kicad_sch]
2025-01-07 moved PCB schematics and layout files to PCB/
    [Battle_bot_pcb.kicad_pcb, Battle_bot_pcb.kicad_sch]
2025-01-08 Set up platfrom io for esp firmware development
    [Battle_bot_pcb.kicad_pcb]
2025-01-08 Added Power multiplexer to schematic
    [Battle_bot_pcb.kicad_pcb, Battle_bot_pcb.kicad_sch]
2025-01-08 Added schottky diode to power multiplexer to protect USB hardware
    [Battle_bot_pcb.kicad_pcb, Battle_bot_pcb.kicad_sch]
2025-01-09 added ESD Protection Diode near MCU
    [Battle_bot_pcb.kicad_pcb, Battle_bot_pcb.kicad_sch]
2025-01-09 Small layout changes
    [Battle_bot_pcb.kicad_sch]
2025-01-09 I/O header
    [Battle_bot_pcb.kicad_pcb, Battle_bot_pcb.kicad_sch]
2025-01-09 small changes
    [Battle_bot_pcb.kicad_pcb]
2025-01-26 Updated layout
    [Battle_bot_pcb.kicad_sch, io.kicad_sch, mcu.kicad_sch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]
2025-01-26 Production files
    [BOM.xlsx, Battle_bot_pcb.kicad_pcb, bom.csv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]
2025-01-27 Added render
    [Battle_bot_pcb.kicad_pcb]
2025-01-28 Updates to README
    [Battle_bot_pcb.kicad_sch, io.kicad_sch, mcu.kicad_sch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]
2025-01-28 moved schematic
2025-01-30 Added pin config and transmission indicatort request led
2025-02-02 Updated motor API to handle motor speed with PWM, and added motor speed control in http post request
2025-02-07 Added photos of manufactured PCB
2025-02-07 Implemented SPI interface for LSM6DS3 and handsake function: Working
2025-02-08 Added init method the IMU spi interface
2025-02-09 Added function for reading LSM6DS3 accelerometer register
2025-02-10 Added function for reading the gyroscope and improved spi code
2025-02-10 Added Sensor API abstraction layer for REST
2025-02-11 Added motor control for api for motor a and b
